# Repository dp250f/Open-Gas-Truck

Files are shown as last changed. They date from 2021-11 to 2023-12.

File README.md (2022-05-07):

# Open-Gas-Truck

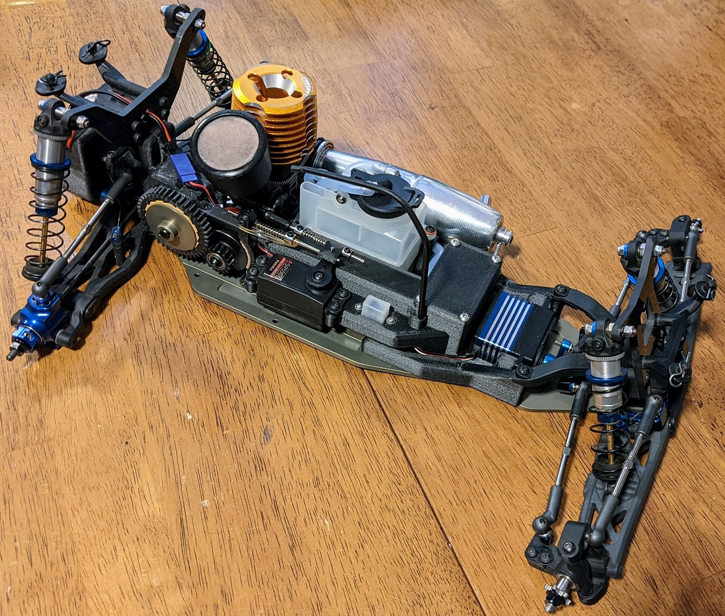
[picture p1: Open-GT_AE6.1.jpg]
Open-GT_AE6.1


The original open-source gas truck conversion

## Associated T6 Series Gas Truck Conversion

There are separate sections and guides for each of these items:

* [3D-Printed parts](3D-Printed)
* [Laser-Cut parts](Laser-Cut-Parts)
* [Modified parts](Modified-Parts)
* [Purchased parts](Purchased-Parts)
* [Assembly](Assembly)

Here's the Fusion 360 (CAD) shares:

* [Full Assembly](https://a360.co/3vGxaeg)
* [Chassis Template Drawing](https://a360.co/3ybymYJ)
* [Laser-Cut Engine Mount Drawing](https://a360.co/3vRHFeG)
* [Laser-Cut Engine Mount Shim Drawing](https://a360.co/3vJ6Rnu)

## Description

How to make your own gas truck conversion. Currently only the Associated T6 platform is done. TLR 22T conversion may happen if I or someone else feels very motivated and has the time to do so.

## Getting Started

First I must say this is a project for experienced makers/hobbyists. There may eventually be ready-to-assemble kit versions, but for now it's DIY only.

### Prerequisites

* 3D printer(s) with the following capabilities (for printing carbon-fiber PA6 Nylon)
    * Hard 0.4mm and 0.25mm nozzle (hardened steel or equivalent)
    * 300°C capable hot-end (make sure you hot-tighten it at that temperature)
    * Heated bed
* Filament dryer
* High quality Carbon-Fiber filled PA6 filament (I used Polymaker Polymide CF-PA6)
* Magigoo or equivalent PA bed adhesive
* Access to a laser cutting service such as send-cut-send
* A T6, 6.1, 6.2, or 6.3 you don't mind sacrificing to the gas truck gods :-)
* Lots of patience and some hacking skills

### Tools

* Printer for printing out chassis modification template
* Center-punch
* Cordless drill
* 3mm and stepped drill bits
* Countersinking bit
* High quality 3mm x 0.5mm tap and tap wrench
* Jigsaw with metal cutting blade
* Assorted files (round and flat)

## Authors

### Contributors names and contact info - *Contributions are welcome!*

* Damon Palm

## Version History

* 0.1
    * Initial Release

## License

This project is licensed under the **GNU General Public License v3.0 License** \- see the [LICENSE File](/LICENSE) for details

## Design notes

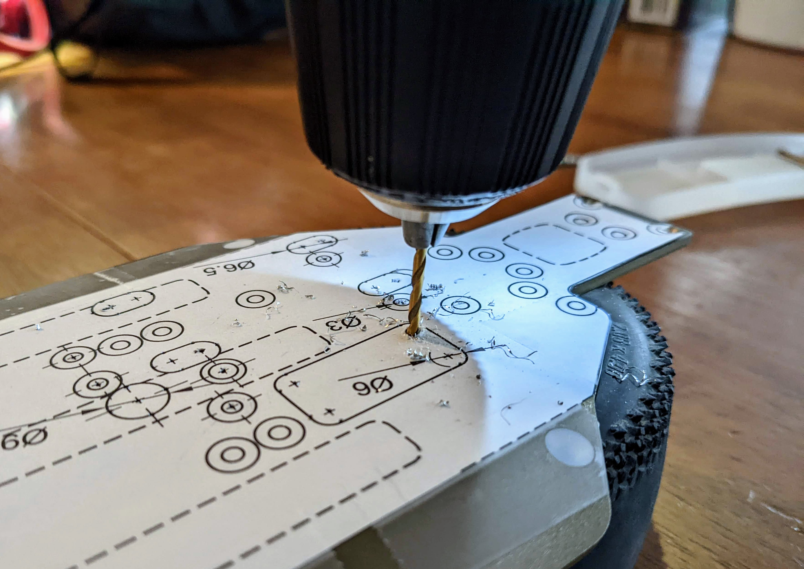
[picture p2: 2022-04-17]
Modified-Parts/Images/Chassis_Drill-1.jpg

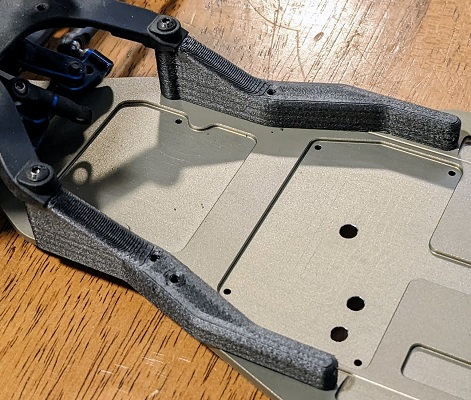
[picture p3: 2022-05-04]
Assembly/Images/FrontChassisBraces.jpg

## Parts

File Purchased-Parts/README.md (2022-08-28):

# Purchased Parts

## Off the shelf parts you will need to complete this build
There are seperate folders and guides for each of these items:

* Associated RC10T6 series truck

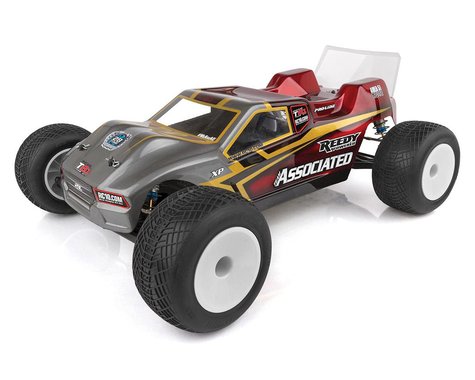
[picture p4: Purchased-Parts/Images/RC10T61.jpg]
RC10T6.1
  
* .12ci (2.1cc) Nitro engine
  * I used an **SH Engines .12 Pro Rear Exhaust Touring Car & Truck Nitro Engine (Turbo Plug)** (SHEPT12R02SXT-1). This is basically the same as the old Dynamite Platinum 12, but with a slide carburetor. It's easy to tune, runs smooth, and has plenty of power for a 2WD truck.

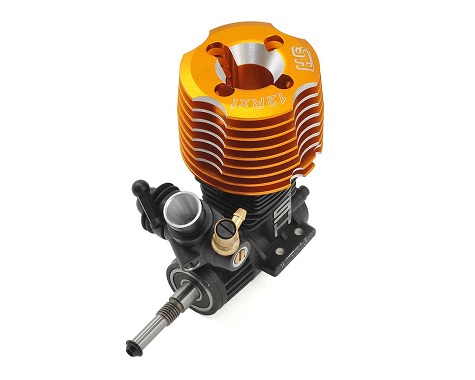
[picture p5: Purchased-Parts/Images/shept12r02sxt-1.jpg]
SHEPT12R02SXT-1
  
* Exhaust header/pipe
  * There are 2 gas truck exhausts currently being made: Ignite RC (IG006) and RD Logics (61900 and 61905). Novarossi still has some new old stock 1/10th pipes which will work with the RD Logics header.

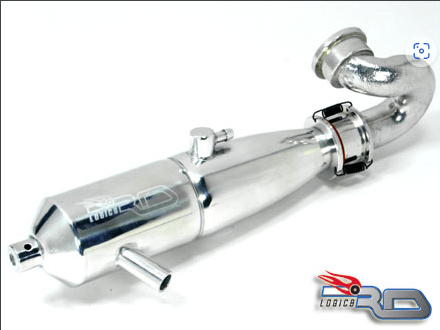
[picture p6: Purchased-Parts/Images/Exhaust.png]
Exhaust
  
* Air filter
  * I used a **Traxxas Complete Air Filter Set (TMX 2.5, 3.3)** (TRA5260). It might seem too large for this carburetor, but the included zip-tie clamps it down good and it seals fine. [Motorsaver.com](https://motorsaver.com/10scale.htm) also has some very nice 1/10th size filters for all sizes of carburetors.

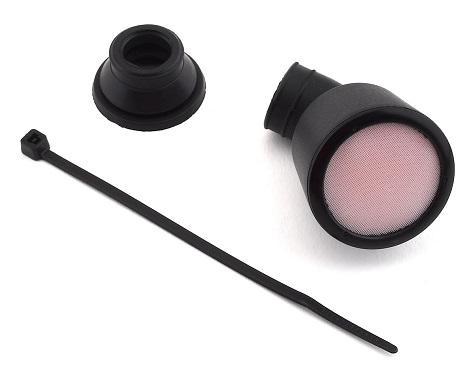
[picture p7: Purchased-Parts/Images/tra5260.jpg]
tra5260
  
* 75cc Fuel Tank (REDCAT 02004) These can be found on Amazon for around $10-$15. Make sure you get a genuine Redcat tank - I've had some cloned tank lids not seal at all.

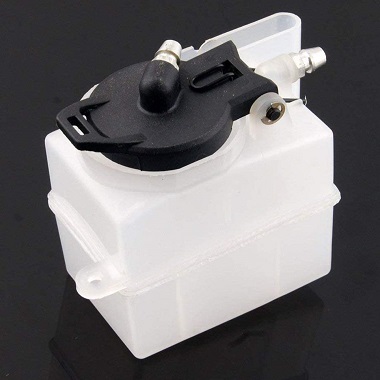
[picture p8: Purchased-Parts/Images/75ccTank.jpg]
75ccTank
  
* Fuel Filter
  * These tanks don't have filters, so this is necessary. I use a small Sullivan "Crap Trap" filter (SUL187).

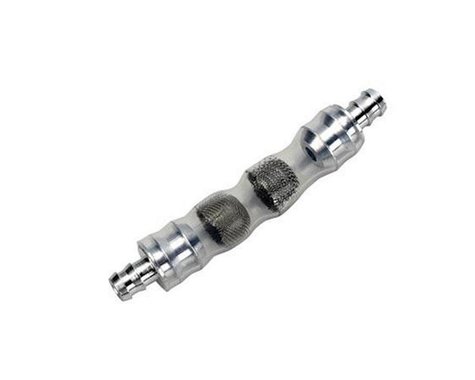
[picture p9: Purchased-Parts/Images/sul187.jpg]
sul187
  
* Standard size silicon fuel line

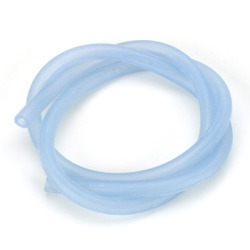
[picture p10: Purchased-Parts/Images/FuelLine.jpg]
FuelLine
  
* 32mm (Kyosho style) 1/8th scale clutch
  * I used a **Fioroni 32mm Quattro "Original RED" 4-Shoe Adjustable Clutch System** (FIO-OT-FR104-R). I've been very happy with this setup, and since it is standard 1/8th stuff, you have lots of tuning options.

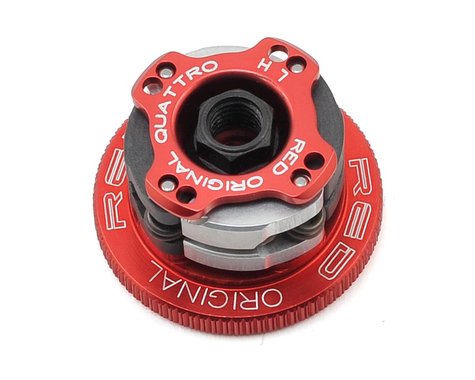
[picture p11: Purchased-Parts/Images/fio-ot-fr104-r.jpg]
fio-ot-fr104-r
  
* 16T Mugen/OFNA style clutch bell
  * I used a **ProTek RC Hardened Clutch Bell w/Bearings (16T) (Mugen/OFNA Style)** (PTK-7053) because it uses HUGE bearings which shouldn't wear out for a very long time.

  ptk-7053
* Team Associated B6.1/B6.1D Standup Top Shaft (ASC91798)

  asc91798
* Team Associated Throttle/Brake Linkage Set (ASC81251)
  * Other similar linkage sets might work, but I really can't say for sure.

  asc81251
* Silicon switch cover
  * I used a **Mugen Seiki Switch Cover** (MUGB0401). Other 1/8th offroad switch covers are likely to work also.

  mugb0401
* Receiver switch
  * I have a Sanwa receiver, so I used a Sanwa switch (SNW107A20064A). Since this kit uses LiPo receiver batteries, a charge plug is not necessary. I just plug the balance plug into my charger.

  snw107a20064a
* Receiver Battery (Mid - for smooth, high-grip tracks) - Mugen/AE/8ight-X style LiPo pack (85 x 30 x 17mm) - (PTK-5196)

  ptk-5196

* Receiver Battery (Rear - for lower-grip tracks) - HB/8IGHT style LiPo pack (39 x 56 x 21mm) - (PTK-5171)

  ptk-5171

* Screws
  * 1 M3x? button head hex screws
  * 1 M3x? countersunk flat head hex screws

* Receiver / Servos (low profile servo for throttle)

## Authors

Contributors names and contact info

So far it's just me here... Contributions are welcome!
Damon Palm

## Version History

* 0.1
    * Initial Release

## License

This project is licensed under the GNU General Public License v3.0 License - see the [LICENSE File](LICENSE) for details

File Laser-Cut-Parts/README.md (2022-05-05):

# Open-Gas-Truck

## Laser-Cut Parts instructions are waiting on parts.

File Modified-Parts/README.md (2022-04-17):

# T6.1 Chassis
## Intro
Time to bust out the center-punch, drill, jigsaw, metal files, and kiss your chassis goodbye!

Make no mistake, you may destroy a perfectly good chassis. Even if everything goes right, you probably won't be using it as an electric chassis again (the rearmost right-side waterfall mount hole is gone).

Basically, you'll be printing out a paper template, taping it to the chassis, marking the holes and cutout with the center-punch and sharpie, and hacking the chassis with power tools. Take your time and you won't need to do it more than once.

## Tools
* Metal center-punch
* Cordless drill or drill press
* 2mm, 3mm and stepped drill bits
* Countersinking bit
* Jigsaw with skinny blade that fits into a 1/4" hole
* Assorted files (round and flat)

## Work
* Download and print the chassis template PDF at 100% scale
* Cut it out and tape it to the bottom of your chassis, making sure existing holes line up
Chassis Template

* Sit the chassis on something solid and use a center-punch to all mark hole centers and edges of larger holes and slots

  Chassis CenterPunch

* Drill all hole centers with smaller drill bit, then drill them to final size with the 3mm drill bit

  Chassis_Drill-2

* Use a stepped drill bit to drill larger holes, engine mount slot ends, and corners of flywheel cutout

  Chassis Drill-3
* Use a countersinking bit to countersink all screw holes. Check fitment of each hole with a screw making sure it sits flush in each hole

  Chassis Screw-Fit
* Use a countersinking bit to deburr both sides of each hole
* Use a sharpie to mark the edges of the flywheel cutout and engine mount slots

  Chassis Countersink
* Use a jigsaw to cut out flywheel hole and engine mount slot edges

  Chassis Saw-2
* Use metal files to smooth and deburr flywheel cutout and engine mount slots

  Chassis File
* sit back and admire your handy work!

## Authors

Contributors names and contact info

So far it's just me here... Contributions are welcome!
Damon Palm

## Version History

* 0.1
    * Initial Release

## License

This project is licensed under the GNU General Public License v3.0 License - see the [LICENSE File](LICENSE) for details

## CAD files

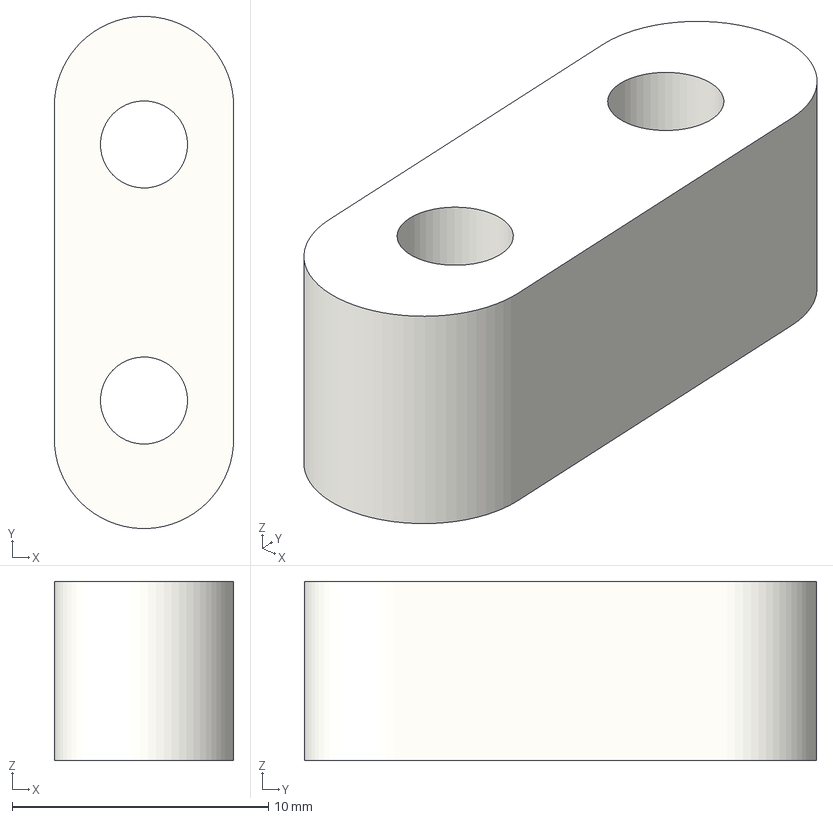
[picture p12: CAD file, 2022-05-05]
3D-Printed/BigNozzle/Throttle Servo Spacer.3mf
7.00 x 20.0 x 7.00 mm

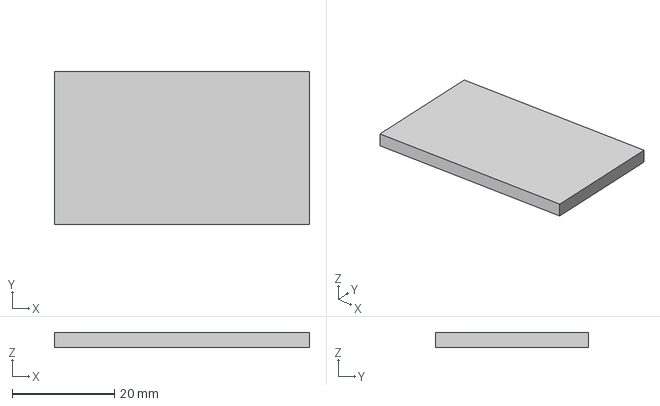
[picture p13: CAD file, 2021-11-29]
3D-Printed/Bridge-Test.3mf
50.0 x 30.0 x 3.00 mm

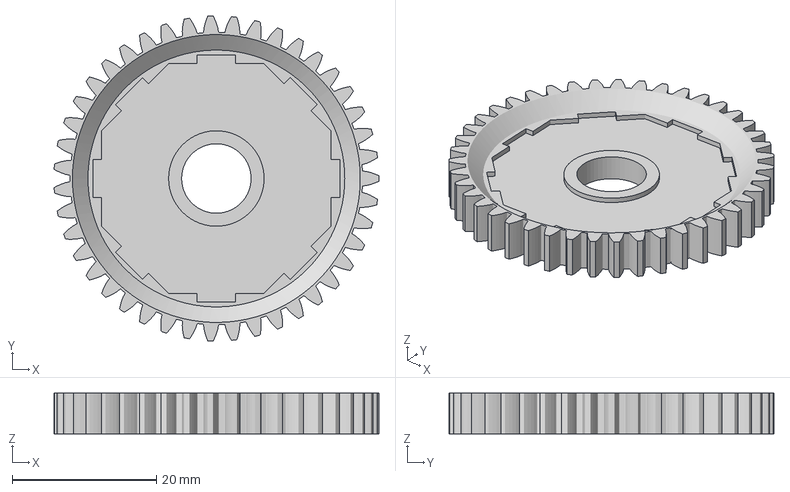
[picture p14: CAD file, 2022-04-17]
3D-Printed/SmallNozzle/Spur Gear (43 teeth).3mf
45.0 x 45.0 x 5.65 mm

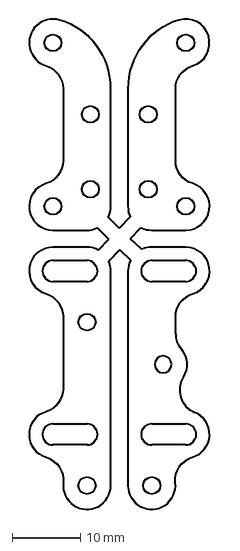
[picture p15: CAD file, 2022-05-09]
Laser-Cut-Parts/Laser-Cut Engine Mounts.dxf
27.1 x 72.6 mm

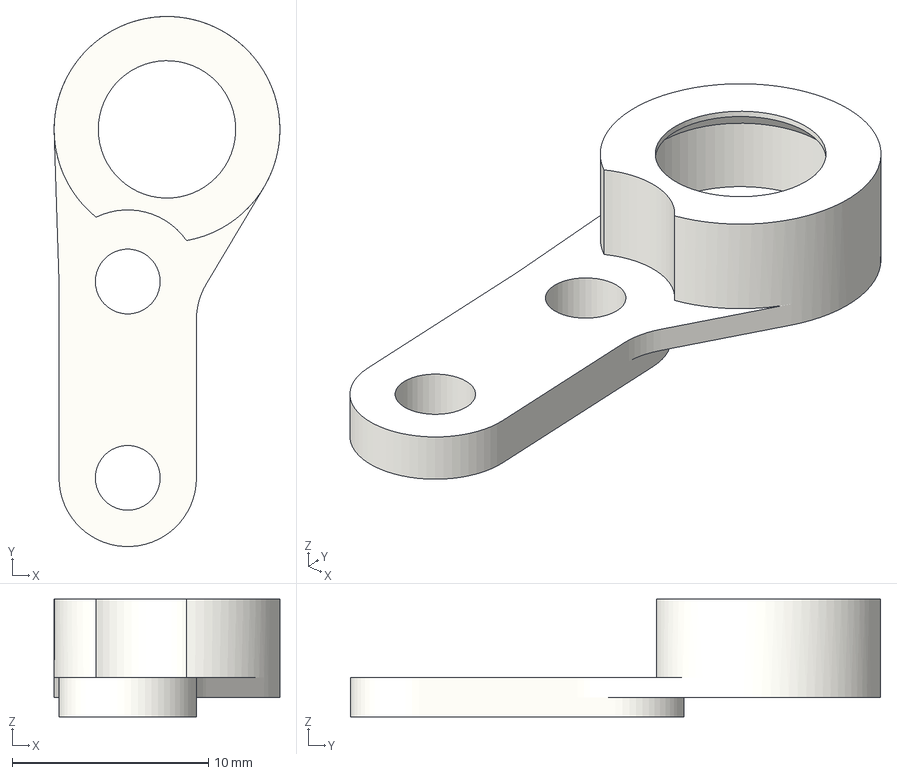
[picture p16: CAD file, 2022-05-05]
3D-Printed/BigNozzle/Spill tube stay.3mf
11.5 x 27.0 x 6.00 mm

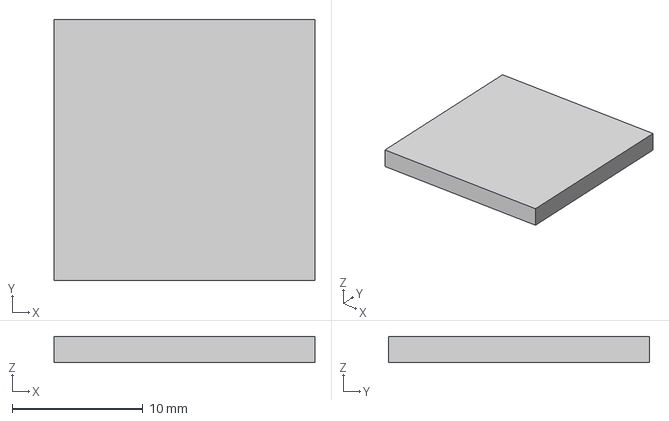
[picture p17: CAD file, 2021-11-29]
3D-Printed/Extrusion-Test.3mf
20.0 x 20.0 x 2.00 mm

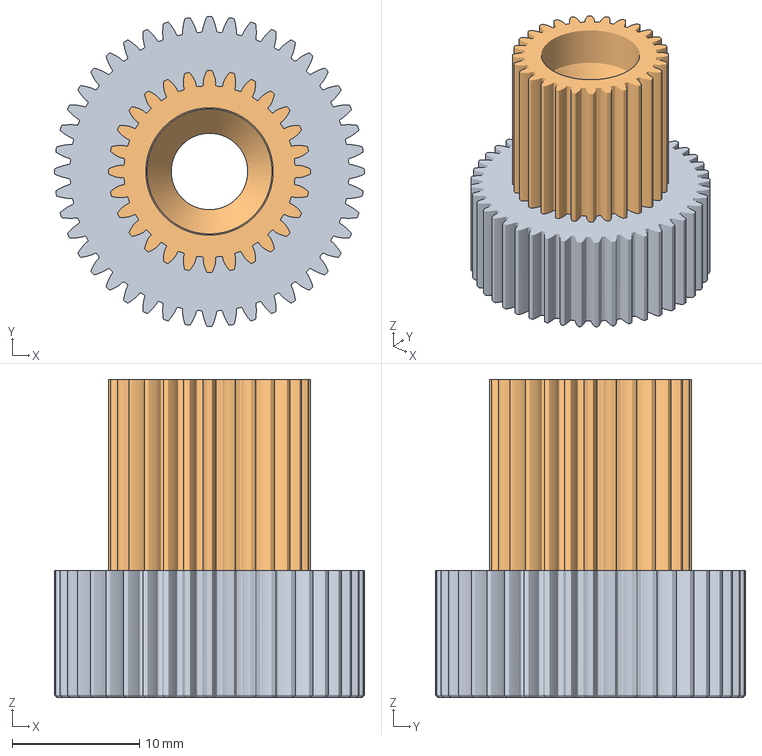
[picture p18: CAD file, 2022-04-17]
3D-Printed/SmallNozzle/Idler Gear.3mf
24.3 x 24.3 x 25.0 mm

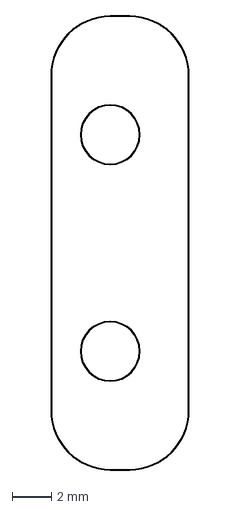
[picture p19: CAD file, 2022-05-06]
Laser-Cut-Parts/Laser-Cut Engine Mount Shim.dxf
7.00 x 23.0 mm

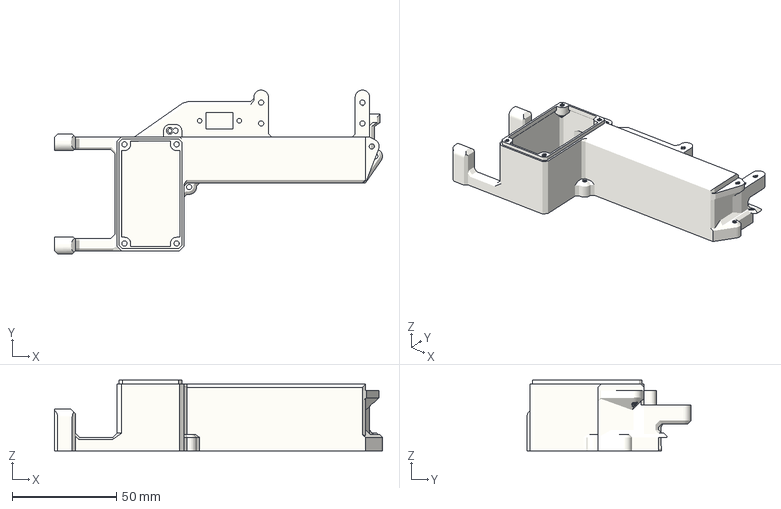
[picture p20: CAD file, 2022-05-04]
3D-Printed/BigNozzle/Electronics tray.3mf
157.1 x 78.5 x 34.0 mm

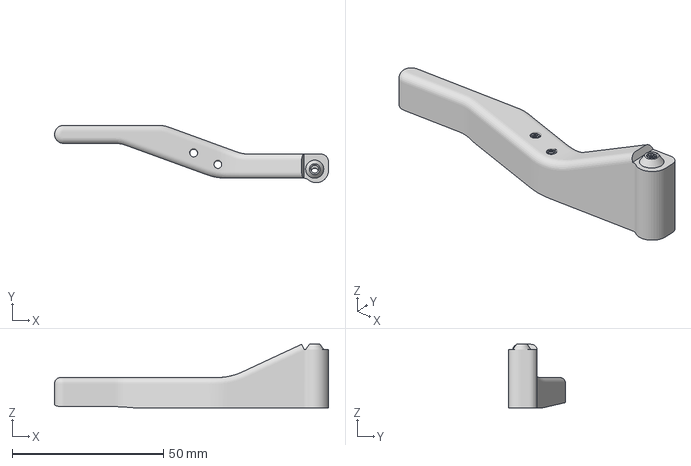
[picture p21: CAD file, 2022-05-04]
3D-Printed/BigNozzle/Front left chassis brace.3mf
90.6 x 19.0 x 21.0 mm

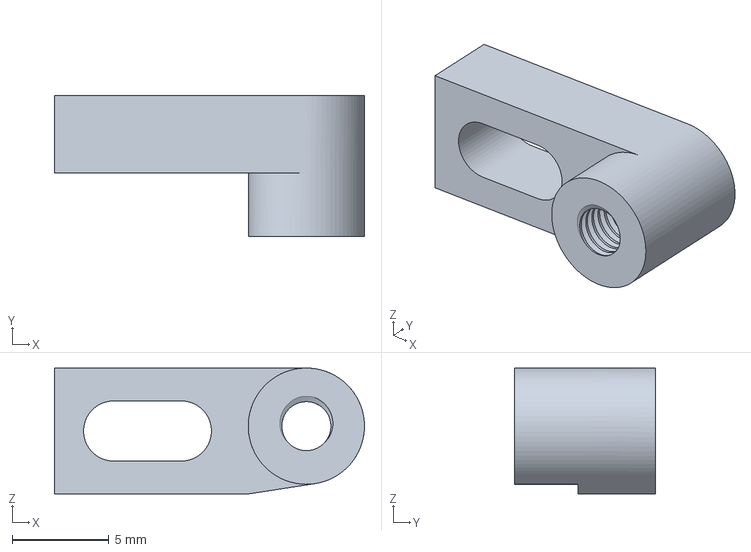
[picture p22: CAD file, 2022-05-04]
3D-Printed/BigNozzle/Brake Mount.3mf
16.0 x 7.27 x 6.50 mm

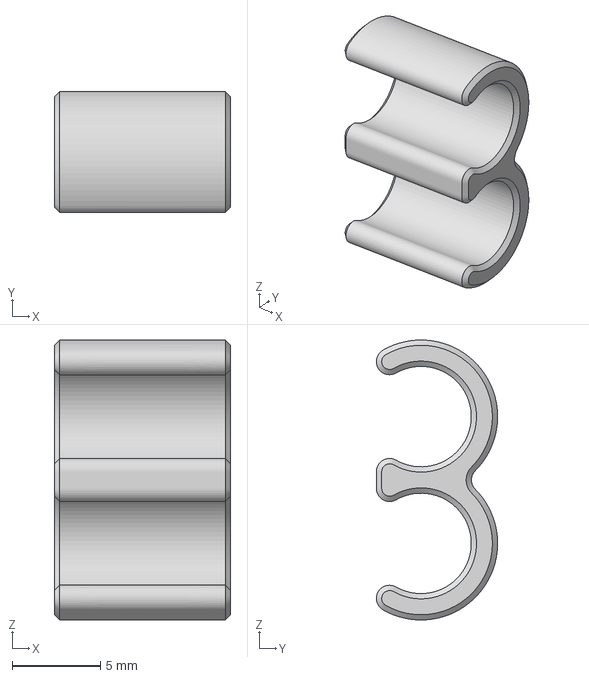
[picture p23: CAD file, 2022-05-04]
3D-Printed/BigNozzle/Fuel line clip.3mf
10.0 x 6.89 x 15.9 mm

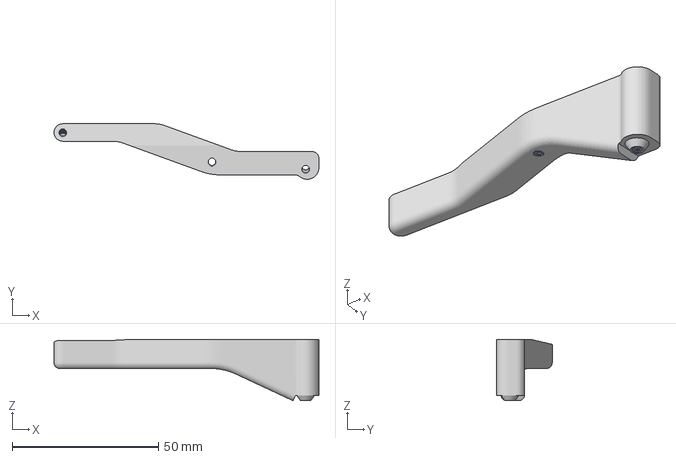
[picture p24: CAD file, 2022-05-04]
3D-Printed/BigNozzle/Front right chassis brace.3mf
90.6 x 19.0 x 21.0 mm

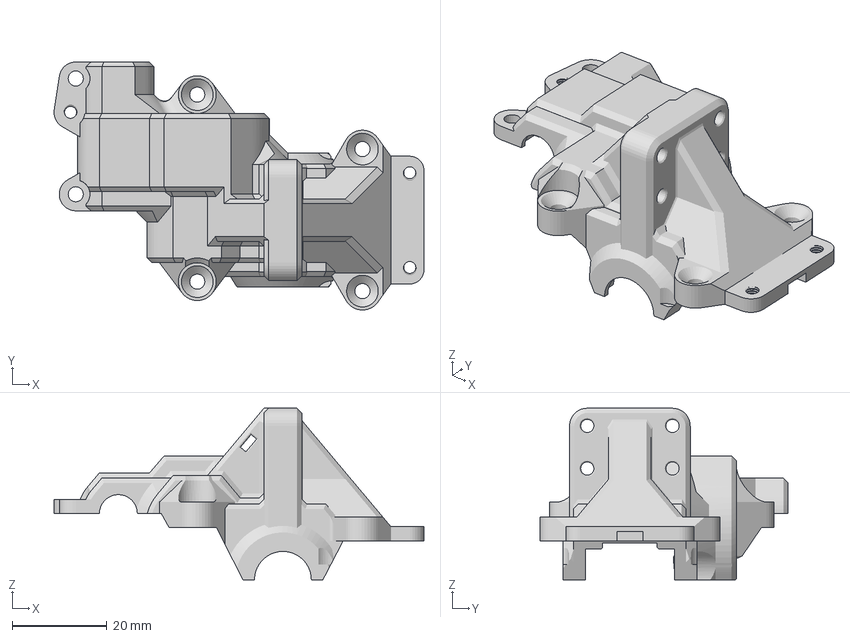
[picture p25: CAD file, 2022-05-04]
3D-Printed/BigNozzle/Transmission top.3mf
78.1 x 52.4 x 36.2 mm

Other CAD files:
3D-Printed/BigNozzle/Servo slider.3mf
3D-Printed/BigNozzle/Rear fuel tank mount.3mf
3D-Printed/BigNozzle/Transmission bottom.3mf
3D-Printed/BigNozzle/Battery box bottom.3mf
3D-Printed/BigNozzle/Battery box top.3mf
3D-Printed/BigNozzle/Chassis Shim.3mf
3D-Printed/BigNozzle/Front fuel tank mount.3mf
3D-Printed/BigNozzle/Receiver Cover.3mf
3D-Printed/BigNozzle/Transmission brace.3mf
3D-Printed/BigNozzle/brake lever.3mf

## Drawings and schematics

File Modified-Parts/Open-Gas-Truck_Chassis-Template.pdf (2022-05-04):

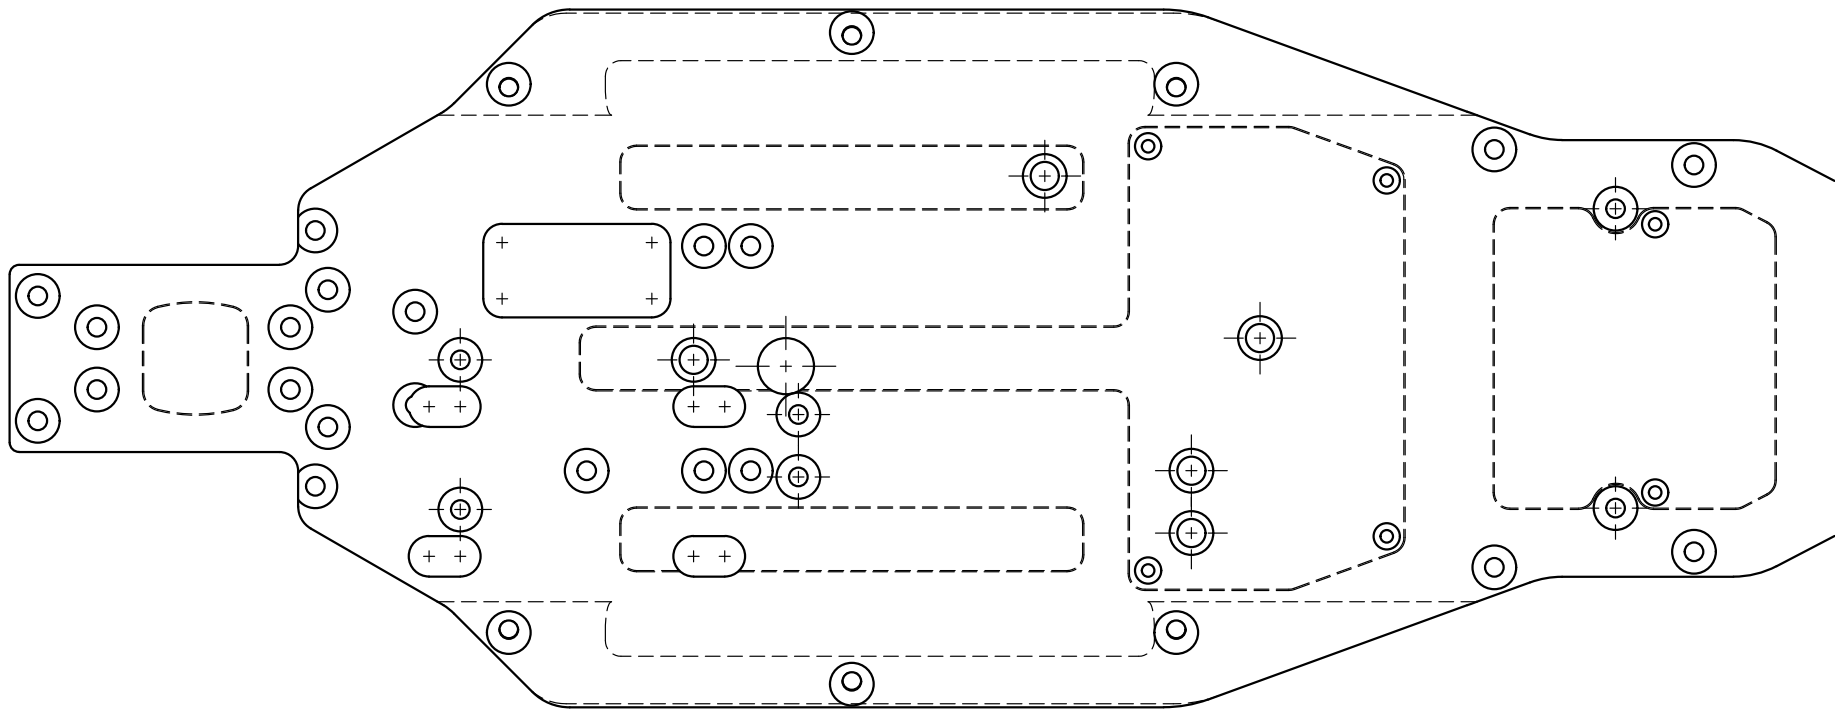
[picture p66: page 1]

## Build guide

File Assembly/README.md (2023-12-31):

# Assembly Guide

## Screw Sizes
Screw lengths are referenced in each step of this guide. Here's how to measure each type of screw
* Countersunk
  * Measure the whole screw

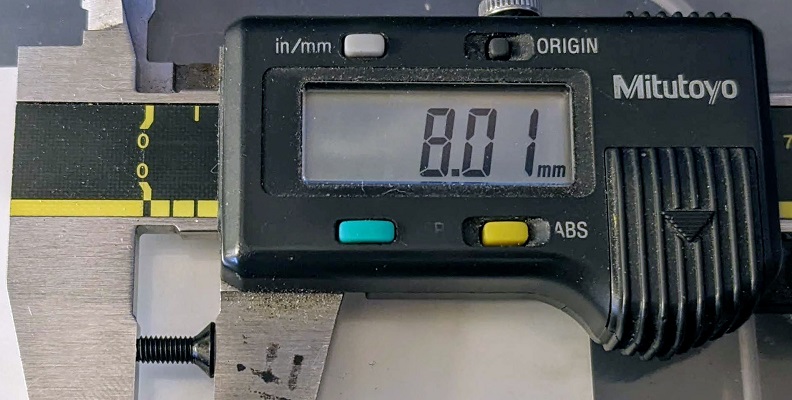
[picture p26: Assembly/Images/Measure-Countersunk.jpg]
Measure-Countersunk
  

* Button Head
  * Measure threads only

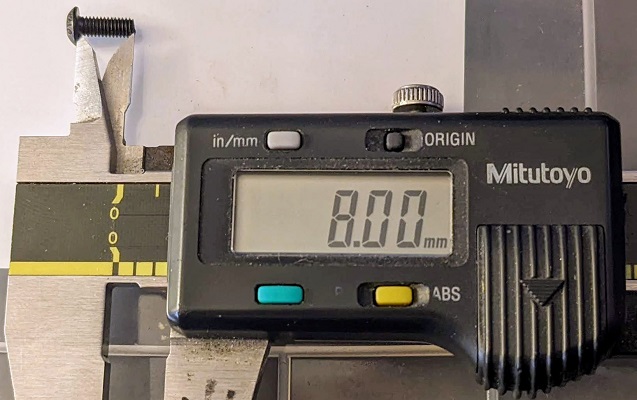
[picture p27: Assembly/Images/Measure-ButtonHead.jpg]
Measure-ButtonHead
  

* Cap Head
  * Measure threads only

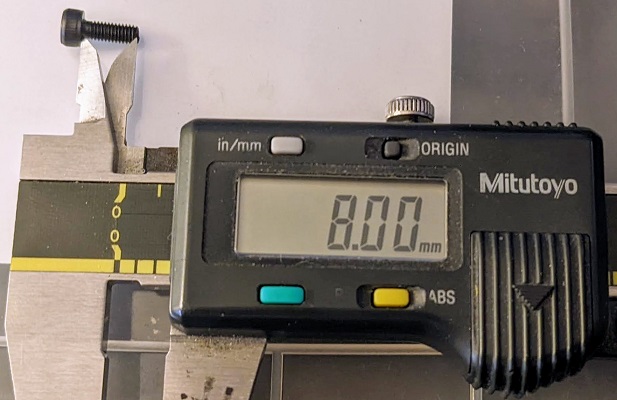
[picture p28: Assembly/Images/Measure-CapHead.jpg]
Measure-CapHead
  

# Front End Assembly

## Install Front Chassis Braces
  * Screws - (4) M3 x 10mm countersunk (front 2 holes)
  * Screws - (2) M3 x 8mm countersunk (rear hole)

## Install Front Clip and Bumper
  * Screws - (4) M3 x 16mm countersunk (bottom)
  * Screws - (2) M3 x 12mm button head (top)

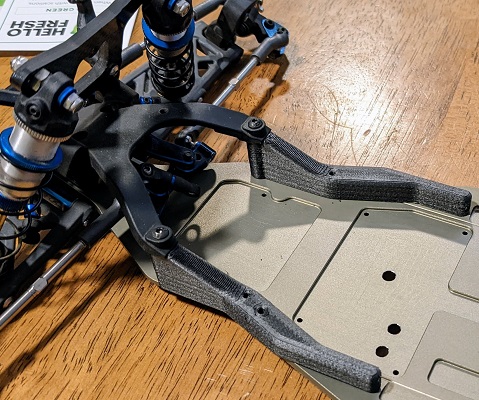
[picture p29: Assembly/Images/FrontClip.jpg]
FrontClip
  

# Rear End Assembly

## Assemble Slipper and Top Shaft
* Insert 3/16 x 3/8 bearing into spur gear

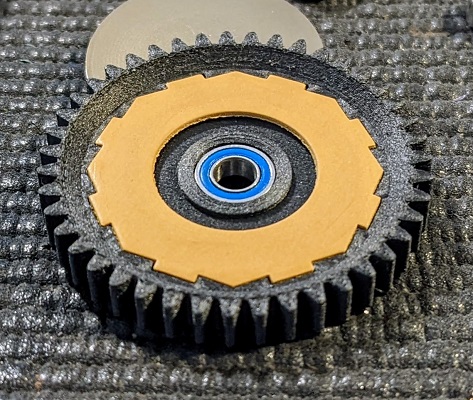
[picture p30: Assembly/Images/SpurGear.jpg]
SpurGear


* Assemble slipper and 3-gear (shorter) top-shaft with spur gear offset facing the inner slipper plate

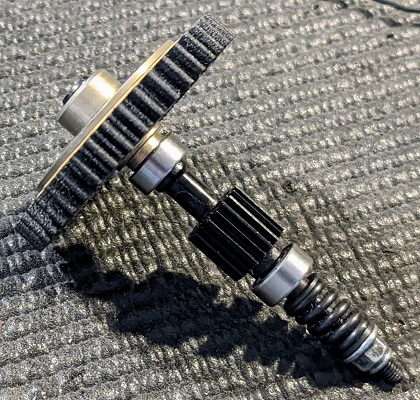
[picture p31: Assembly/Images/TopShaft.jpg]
TopShaft


## Assemble Transmission
  * Screws - ( 1) M2.5 x 8mm countersunk
* Install camber link block in bottom transmission case

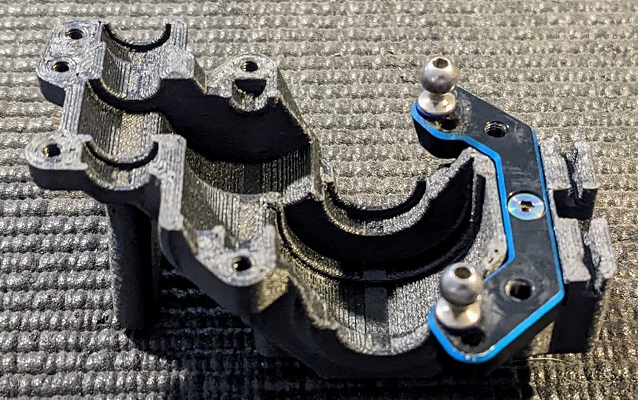
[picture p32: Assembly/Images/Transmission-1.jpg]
Transmission-1


* Install idler shaft and 5x10x4 bearings into idler gear

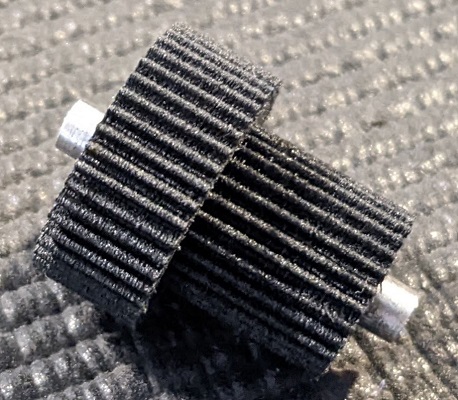
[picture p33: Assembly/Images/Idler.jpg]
Idler


* Install differential, idler, top-shaft, and swaybar in bottom transmission case and grease gears with black grease

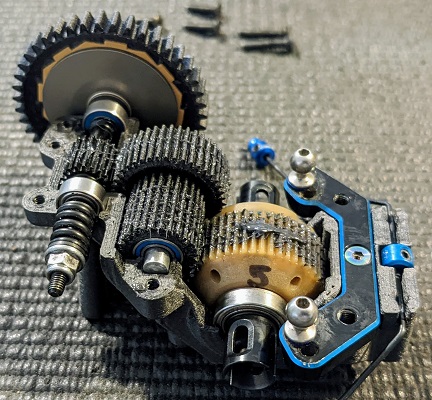
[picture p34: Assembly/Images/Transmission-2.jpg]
Transmission-2


  * Screws - (2) M3 x 16mm countersunk (rear)
  * Screws - (2) M3 x 12mm countersunk (middle)
  * Screws - (2) M3 x 8mm button head (front)
* Install top transmission case and screws

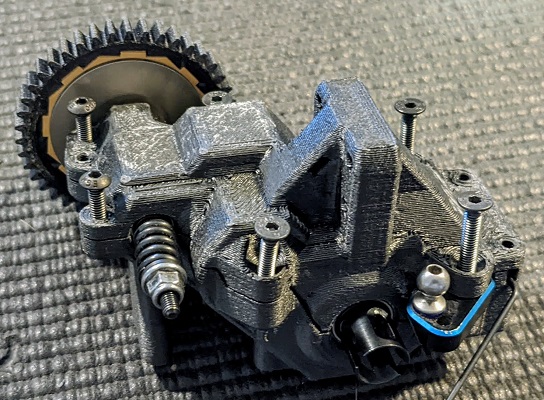
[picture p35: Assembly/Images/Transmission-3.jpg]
Transmission-3


## Install C-Block
  * Screws - (2) M3 x 6mm countersunk

## Install Transmission and Rear Shock Tower
  * Screws - (3) M3 x 10mm countersunk (front 3 transmission screws)
  * Screws - (4) M3 x 12mm button head (shock tower)
    
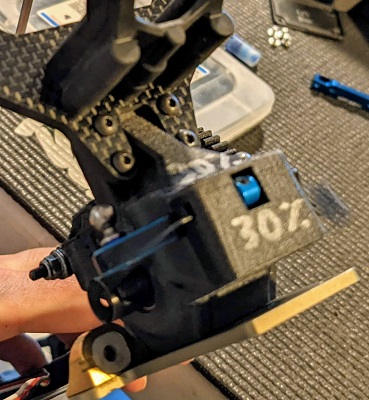
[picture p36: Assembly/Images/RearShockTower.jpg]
RearShockTower


## Install Transmission and Suspension (Mid-Battery Option)    
  * Screws - (2) M3 x 16mm countersunk (rear D-Block screws)
  * Screws - (2) M3 x 6 button head (swaybar screws)
* Secure D-Block and bumper using 16mm countersunk screws.
* Insert swaybar screws far enough to take slop out of the swaybar while allowing it to swing freely

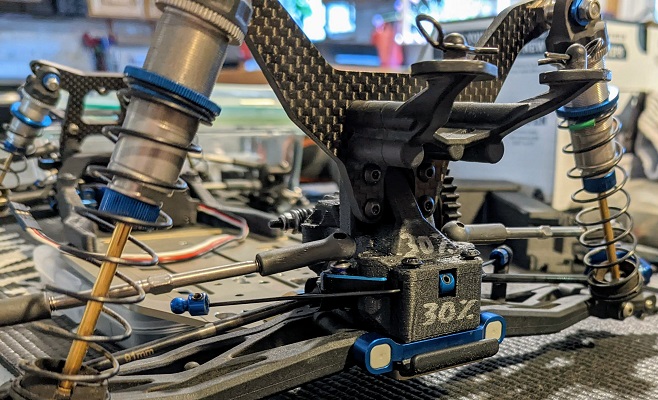
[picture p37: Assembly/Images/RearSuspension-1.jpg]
RearSuspension-1


## Assemble Rear Battery Box (Rear-Battery Option)
* Wrap a layer of tape around the battery as needed to protect the shrink wrap and insert battery into top of battery box

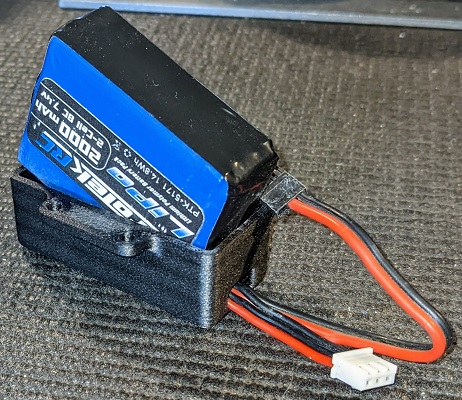
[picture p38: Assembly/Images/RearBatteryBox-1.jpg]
RearBatteryBox-1


  * Screws - (2) M3 x 8mm button head
* Screw battery box together

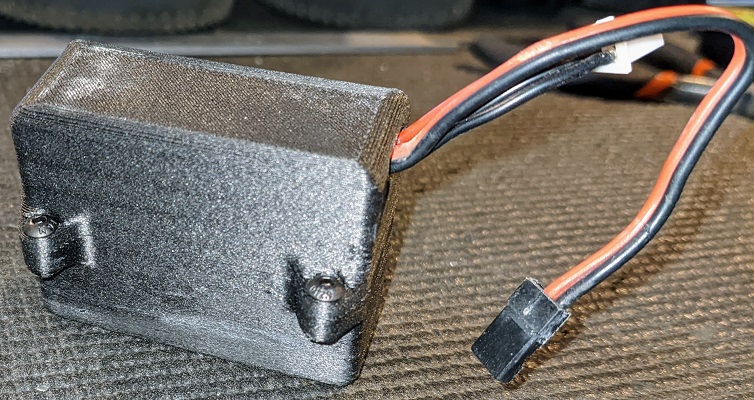
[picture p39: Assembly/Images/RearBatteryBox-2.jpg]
RearBatteryBox-2


## Install Rear Battery Box (Rear-Battery Option)
  * Screws - (2) M3 x 16mm countersunk (rear D-Block screws)
  * Screws - (2) M3 x 8 button head (top battery box mount)
* Attach bottom battery box where bumper normally goes using 16mm countersunk screws
* Use 8mm button head screws to secure top battery box in swaybar screw holes. These should get tight enough to take slop out of the swaybar while allowing it to swing freely while securing the battery box

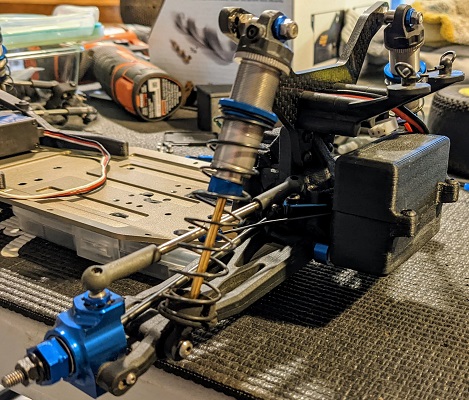
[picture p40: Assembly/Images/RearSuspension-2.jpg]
RearSuspension-2


# Electronics Tray Assembly

## Chassis Shims
* Glue chassis shims countersunk side down onto the 2 middle mounting holes as shown in the next step

## Install Mid Battery (Mid-Battery Option)
* Wrap a layer of tape around the battery as needed to protect the shrink wrap and insert battery into mid battery compartment

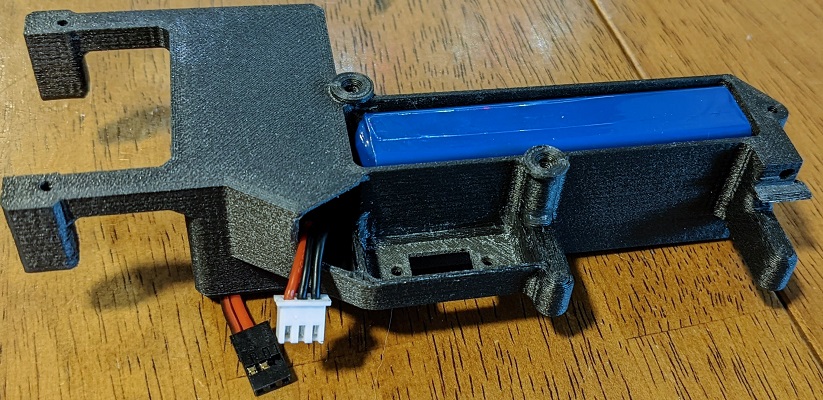
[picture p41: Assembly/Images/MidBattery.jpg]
MidBattery


## Install Steering Servo
  * Screws - (2) M3 x 10mm button head (top screws)
  * Screws - (2) M3 x 8 button head (bottom screws)
* Bottom side of servo should be flush or slightly higher than the bottom surface of the electronics tray

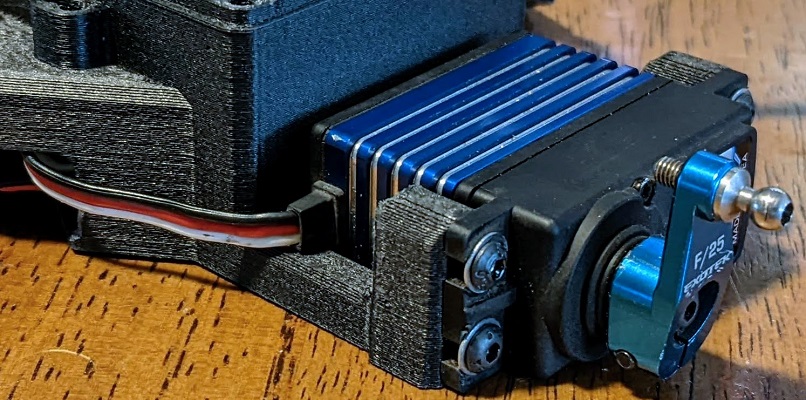
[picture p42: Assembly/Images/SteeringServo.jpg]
SteeringServo


## Install Switch and Throttle Servo
  * Switch screws - (2) whatever the switch came with
  * Screws - (4) M3 x 8-10mm button head (short throttle servo)
  * Screws - (4) M3 x 16mm button head (tall throttle servo)
    * Use Throttle Servo Spacers if using a tall servo
* Servo wire can tuck behind switch
* Switch wire tucks behind throttle servo (rear battery option)

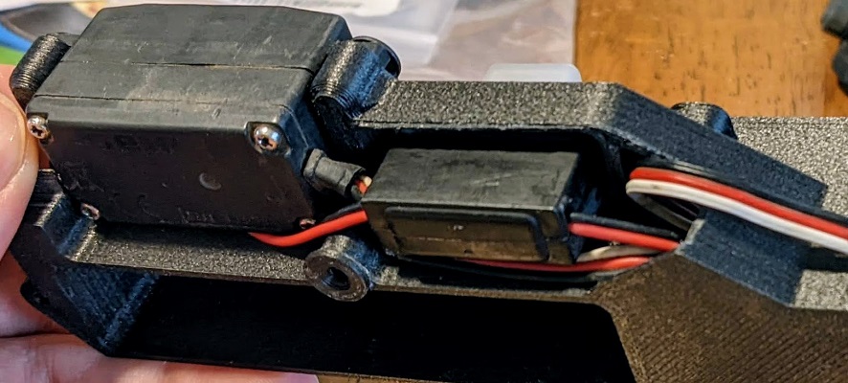
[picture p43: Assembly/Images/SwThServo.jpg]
SwThServo


## Install Receiver, transponder, antenna tube
  * Screws - (4) M3 x 6mm button head (receiver box cover)
  * Screws - (1) M3 x 4 set screw (antenna tube)
* Insert a layer of open cell foam in the bottom of the receiver box
* Plug switch, servos, and transponder into receiver

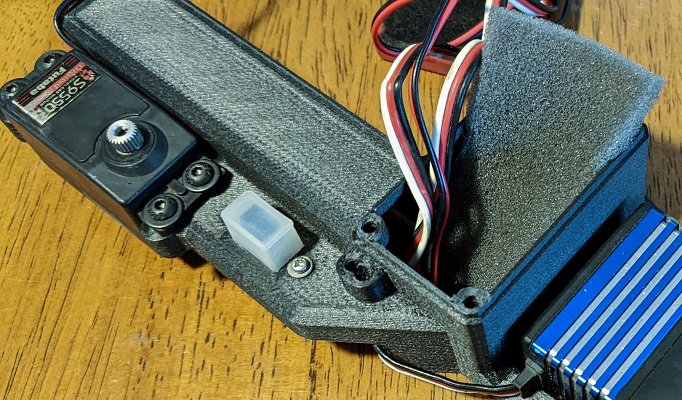
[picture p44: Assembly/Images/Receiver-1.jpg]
Receiver-1


* Feed antenna wire through antenna hole leaving enough slack to remove receiver from receiver box
* Feed antenna into antenna tube and install it using set screw
* Insert receiver, fold wires on top
* Insert transponder on top of wires

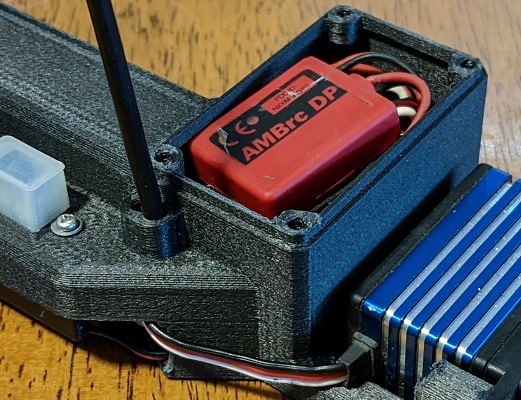
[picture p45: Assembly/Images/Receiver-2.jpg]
Receiver-2


* Insert a layer of open cell foam on top of transponder
* Install receiver box cover using button head screws

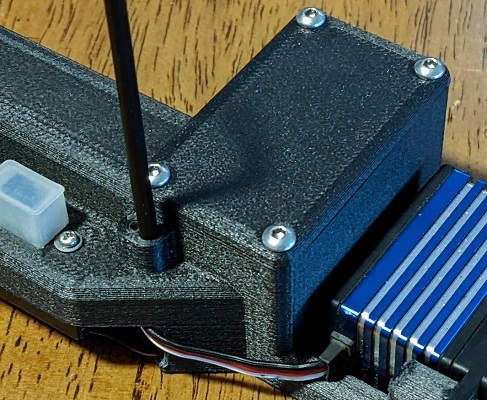
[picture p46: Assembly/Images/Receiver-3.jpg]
Receiver-3


## Assemble brake
  * Screws - (1) M3 x 16mm button head (brake arm)
  * Screws - (1) M3 x 12mm button head (brake mount)
* Cut out and glue 1/16" thick piece of cork onto brake arm (This is the brake pad)
* Drill brake linkage hole with 2mm drill bit (so a 2mm screw can rotate freely in it)

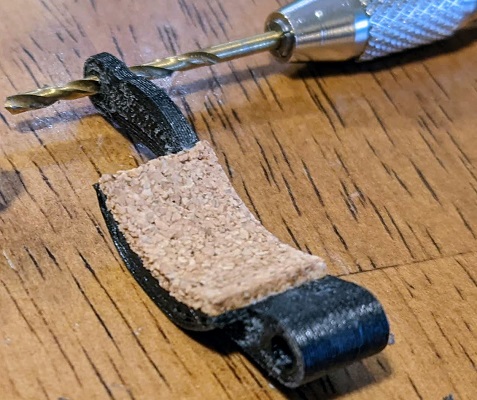
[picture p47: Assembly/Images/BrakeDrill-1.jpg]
BrakeDrill-1


* Drill brake pivot hole with 3mm drill bit (so a 3mm screw can rotate in it, but have almost no slop)

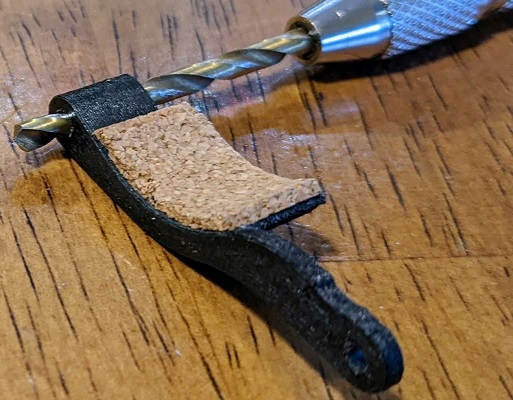
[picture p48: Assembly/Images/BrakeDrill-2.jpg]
BrakeDrill-2


* Assemble brake arm and brake mount using M3 x 16mm button head screw (Leave it loose enough to freely rotate)

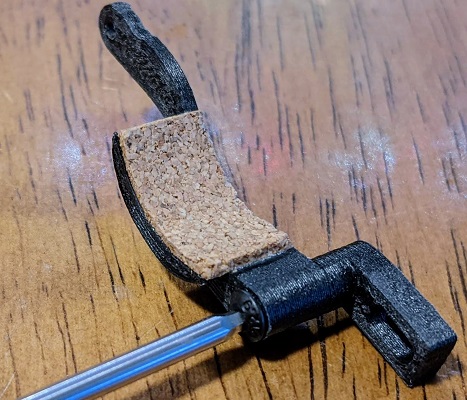
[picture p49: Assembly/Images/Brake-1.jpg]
Brake-1


* Assemble brake mount to electronics tray using M3 x 12mm button head screw (Leave it loose enough to be able to adjust the mount)

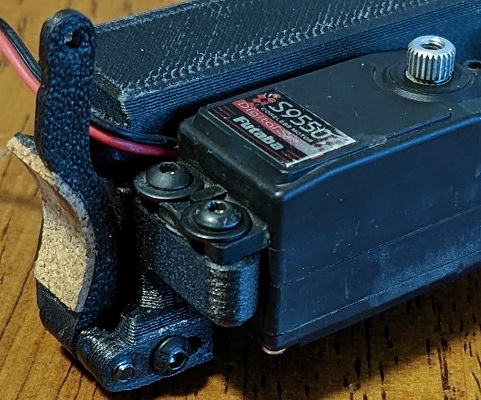
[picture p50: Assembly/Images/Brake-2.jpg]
Brake-2


# Center Chassis Assembly

## Install Electronics Tray
  * Screws - (5) M3 x 10mm countersunk
* Install electronics tray in chassis using countersunk screws
* Snap steering link ballcup onto servo arm ballstud

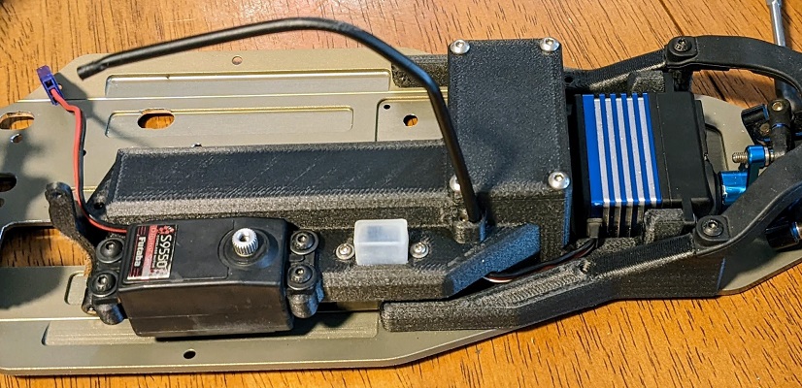
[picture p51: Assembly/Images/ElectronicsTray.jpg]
ElectronicsTray


## Install Transmission Brace
  * Screws - (2) M3 x 10mm countersunk
* Thread receiver switch wire and transmission brace through large heat shrink tubing (Rear battery option)
* Install transmission brace using countersunk screws
* Adjust slack in receiver switch wire, leaving room for brake lever to move all the way forward (Rear battery option)
* Shrink heatshrink using heat gun (Rear battery option)
* Secure receiver battery wire using small wire tie (Rear battery option)

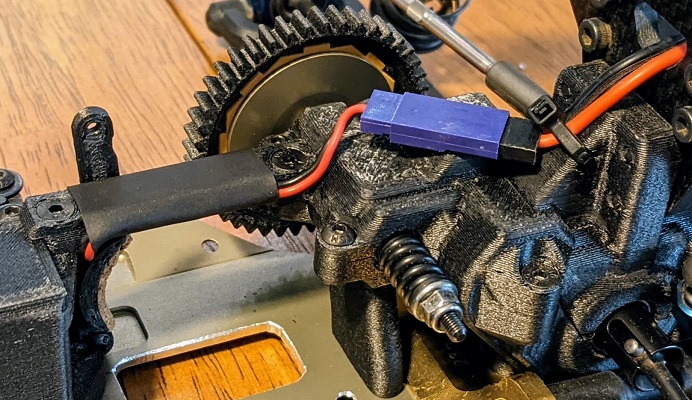
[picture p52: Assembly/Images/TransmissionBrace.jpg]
TransmissionBrace


## Install Fuel Tank
  * Screws - (2) M3 x 16mm button head (top fuel tank mounts)
  * Screws - (2) M3 x 8mm countersunk (fuel tank mount joiner)
  * Screws - (2) M3 x 12mm countersunk (fuel tank mount chassis screws)
  * O-Rings - (6) 1/10th scale shock o-rings (the kind that fit 3mm shock shafts)
* Cut slots in fuel tank lid to allow it to open all the way without bending the spring

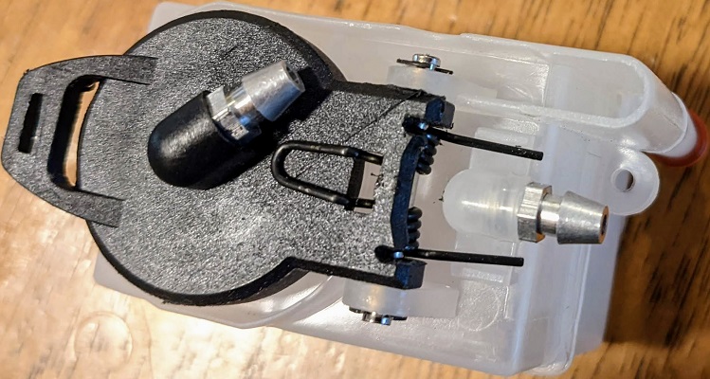
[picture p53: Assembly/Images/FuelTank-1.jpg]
FuelTank-1


* Drill mount holes with 3mm or 1/8" drill

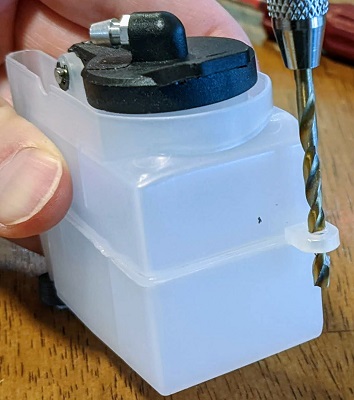
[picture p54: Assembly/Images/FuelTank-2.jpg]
FuelTank-2


* Install spill tube o-ring and spill tube stay

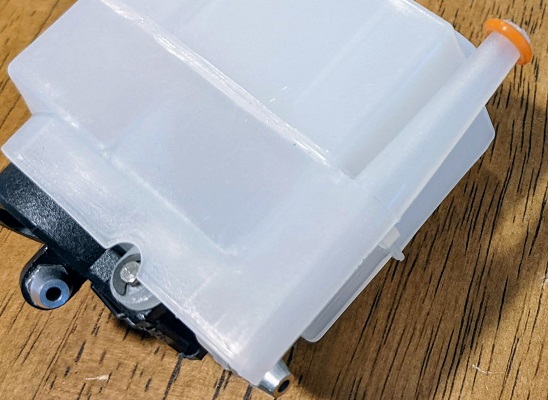
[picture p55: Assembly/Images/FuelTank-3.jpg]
FuelTank-3

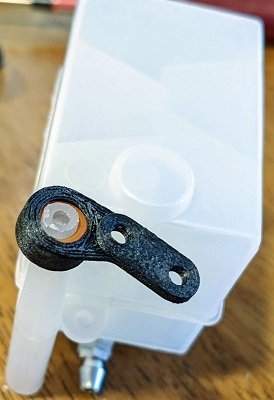
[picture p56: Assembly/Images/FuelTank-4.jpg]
FuelTank-4


* Attach front mount to tank using 16mm button head screw, 3 o-rings (2 bottom, 1 top), and washer
* Attach rear mount to tank using 12mm button hear screw, 2 o-rings, and washer

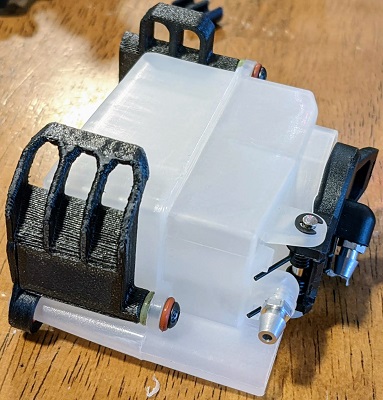
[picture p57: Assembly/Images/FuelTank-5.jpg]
FuelTank-5


* Attach tank mount joiner to tank mounts using (2) countersunk screws

* Install fuel tank in chassis using (2) countersunk screws

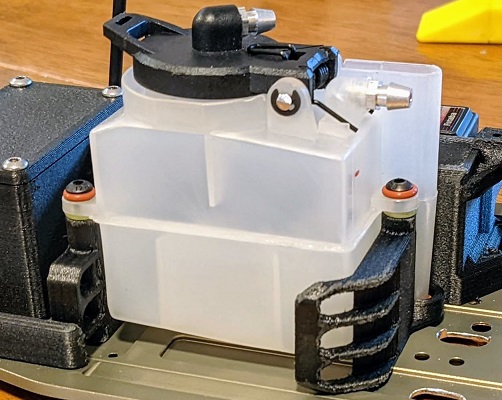
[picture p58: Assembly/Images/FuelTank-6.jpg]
FuelTank-6


# Engine Installation

## Assemble Engine, Clutch, and top Engine Mounts
  
  * Screws - (4) M3 x 12mm cap-head
* Install carburetor with slide facing the engine's left side and fuel fitting facing the rear of the engine
* Install clutch and clutch bell per clutch manufacturer's instructions
* Install throttle return elastic band
* Install air filter
* Install top engine mounts and shims as shown below using cap head screws **\*Use Threadlock**

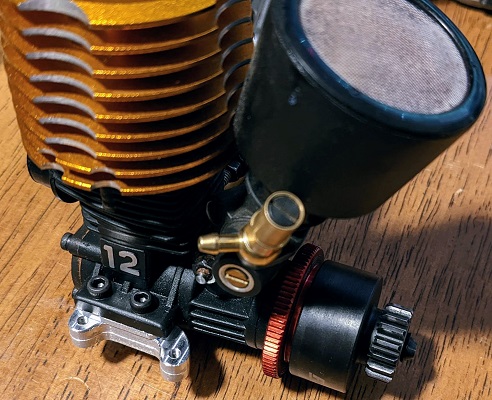
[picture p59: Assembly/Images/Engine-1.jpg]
Engine-1


## Install Bottom Engine Mounts

  * Screws - (4) M3 x 8mm countersunk
* Glue chassis shim to bottom front engine mount as shown below

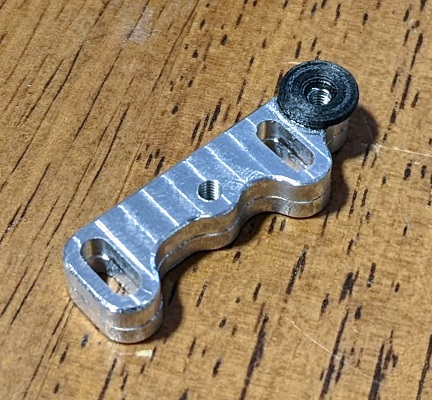
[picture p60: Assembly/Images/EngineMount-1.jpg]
EngineMount-1


* Install bottom engine mounts using countersunk screws **\*Use Threadlock**

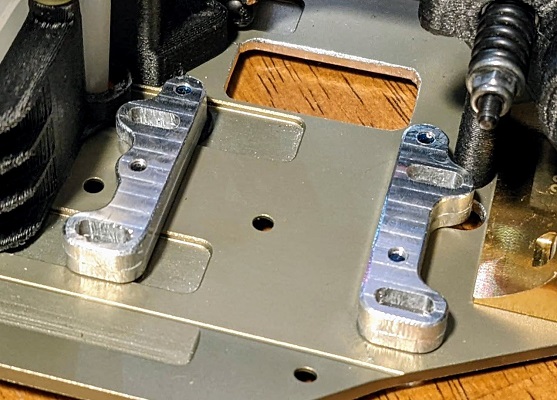
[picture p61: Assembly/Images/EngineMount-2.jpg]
EngineMount-2


## Install Engine, Fuel Line, Exhaust

  * Screws - (4) M3 x 12mm cap head
* Install engine using cap head screws from the bottom of the chassis
* Set gear mesh 
* **Threadlock** cap head screws one at a time
* Adjust brake and tighten brake mount screw

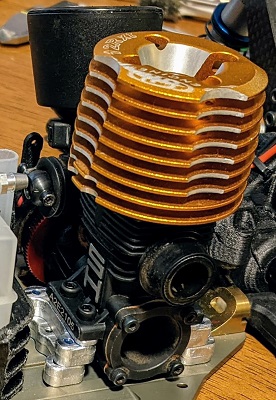
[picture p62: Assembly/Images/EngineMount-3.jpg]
EngineMount-3

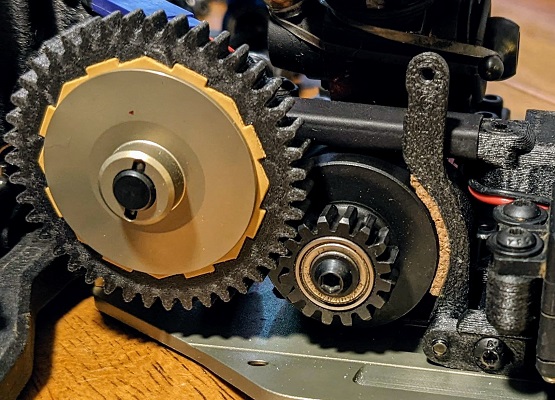
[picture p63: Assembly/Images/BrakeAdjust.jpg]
BrakeAdjust


* Install fuel line and fuel filter leaving enough free pressure line to connect the pipe later

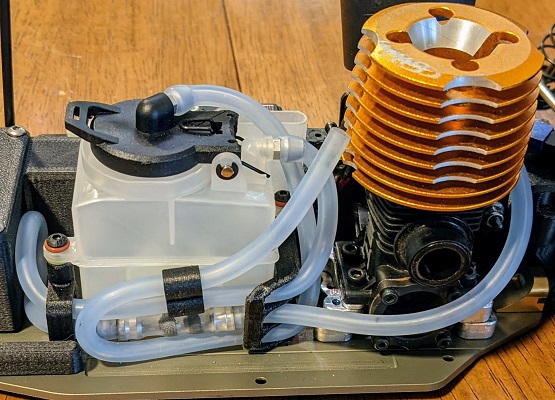
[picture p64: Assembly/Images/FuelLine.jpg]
FuelLine


  * Screws (1) M3 x 12mm button head
* Install Exhaust manifold and pipe. Secure pipe hanger wire with button head screw and washer

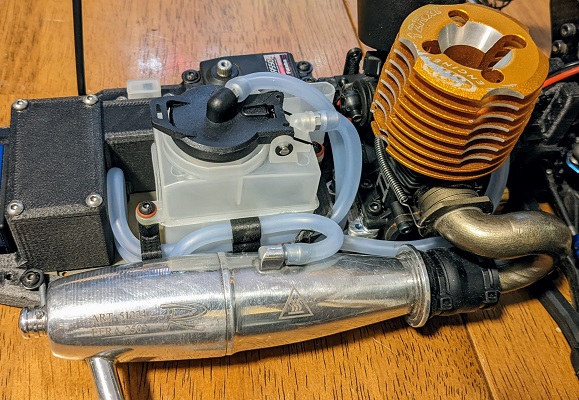
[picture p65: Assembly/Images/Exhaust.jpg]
Exhaust


## Install Throttle Linkage
  * Screws (2) M2 linkage screws (long and short)
* Drill out one throttle slider hole so your linkage slides freely through it.
* Attach throttle slider on top side of throttle servo arm (short servo option)
* Attach throttle slider on bottom side of throttle servo arm (tall servo option)
    * Leave it loose enough so it rotates freely on the arm.

Throttle-1

* Turn on Transmitter and receiver and center all throttle trims.
* Assemble throttle and brake linkage as shown below
* Throttle link slides through throttle slider. Use stiffer spring(s) on this one
* Brake link threads into throttle slider

Throttle-2
Throttle-3

https://github.com/dp250f/Open-Gas-Truck/assets/33988652/a270fac0-811a-4a7e-be5f-dab042d3d477

# 
## Authors

Contributors names and contact info

So far it's just me here... Contributions are welcome!
Damon Palm

## Version History

* 0.1
    * Initial Release

## License

This project is licensed under the GNU General Public License v3.0 License - see the [LICENSE File](LICENSE) for details

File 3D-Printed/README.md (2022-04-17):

# 3D Printed parts guides

## Description

Different types of parts have their own guides:

* *[0.4mm nozzle](BigNozzle/README.md)*
* *[0.25mm nozzle](SmallNozzle/README.md)*

## Prerequisites

The sizing of these parts and this guide assume you'll be using PrusaSlicer. You are free to use whatever slicer you want, but be warned - You'll be on your own to figure out what settings work. I started out using Cura, but couldn't get support material to work well while being reasonably easy to remove.

* 3D printer(s) with the following capabilities (for printing carbon-fiber PA6 Nylon)
    * Hard 0.4mm and 0.25mm nozzle (hardened steel or equivalent)
    * 300°C capable hot-end (make sure you hot-tighten it at that temperature)
    * Heated bed
* Filament dryer
* High quality Carbon-Fiber filled PA6 filament (I used Polymaker Polymide CF-PA6)
* Magigoo or equivalent PA bed adhesive

# Before printing parts...

Save yourself from future headaches by drying your filament and doing some tuning. This material prints very different than PLA. It's also expensive, so these test prints are pretty minimal.

## Tune Extrusion Multiplier

Because CF-Nylon likes to absorb moisture, it's nearly impossible to keep it completely dry without storing it in a vacuum chamber. I've also found my E-steps are off compared to PLA likely due to how hard this stuff is. Rather than throw off E-steps for printing other types of filament, it's easier to tune extrusion multiplier for this material (you'll need to even if you do re-tune your E-steps).
Extrusion Multiplier test prints

* Print small 20x20x2 calibration cubes at 100% infill to determine what multiplier to use. Make sure you use the same extrusion width, layer height, and infill/skin overlap settings you will be using to print your parts. (It shouldn't matter, but slicers be weird like that) You want a smooth top surface with no gaps and just a little bit of roughness that you can see and feel with your fingernail around the edges of the infill where it overlaps the perimeters.
* This can vary depending on how dry your filament is. 0.86 (or 86%) is the multiplier I ended up using after it's been out of the vacuum sealed packaging for a day or so (I don't have a vacuum chamber to store it in). In theory, if you can get this stuff completely dry and re-tune your E-steps, it'll be 1.00. I've never bene able to get higer than 0.87 with my filament dryer. I always store it in a sealed bag with desiccant in the box it came in and always print from the filament dryer (and leave it in there all day every time I do). I've found if I can't use at least 0.85 extrusion multiplier, that means it's too wet, will ooze like crazy and not have good layer adhesion.
* Dimensional accuracy is less important for most parts while layer adhesion is most important, so err on the side of over-extrusion.

## Tune Bridge Flow Ratio

CF-Nylon doesn't seem to exhibit die-swell and shrinking like PLA does, which makes bridging more difficult. Excellent bridging can still be accomplished with CF-Nylon, but it requires a much lower flow ratio than you're used to. It can also re-melt and warp/sag the bridging layer when printing the next layer - but there's a workaround for that which we should only need to use for printing the spur gear.
Bridge Flow Ratio test prints (Top)
Bridge Flow Ratio test prints (Bottom)
These were printed at 30mm/s bridge speed. First number is flow ratio percent and 2nd number is fan speed. The top piece is without bridge cooling for reference.

* Print 30x50x3 bridging test cubes with 0% infill and no support, 0 bottom layers, 2 top layers and 3 perimeters.
* Try different speeds and flow ratios with 100% bridge fan speed. Usually 20mm/s-30mm/s and 40%-70% flow ratio.
* I like to stop the test print a little more than half-way through the last layer so I can see both the bridging layer by itself and with the next layer on top of it.
* You want a flow ratio which produces the smoothest and flattest bridge and top layer as possible. In these pictures you can see that's probably somewhere around 55%-60%

## Authors

### Contributors - *Contributions are welcome!*

* Damon Palm

## Version History

* 0.1
    * Initial Release

## License

This project is licensed under the **GNU General Public License v3.0 License** \- see the [LICENSE File](/LICENSE) for details

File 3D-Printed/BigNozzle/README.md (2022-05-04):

# 0.4mm Nozzle Parts

## Material / part requirements:

* Carbon-Fiber PA6 Nylon (Polymaker Polymide CF-PA6)
* Filament dryer which can dry Nylon
* 0.4mm hardened nozzle at 300°C
* Magigoo PA on 45°C bed
* Print each part one at a time to keep the layer time as short as possible. This makes layer adhesion as strong as possible.

## Slicer settings:

Assuming your hot end is up to the task of printing abrasives at 300°C and you've got a filament dryer capable of drying Nylon, printing CF-PA6 Nylon isn't too tricky. The sizing of these parts and this guide assume you'll be using PrusaSlicer. 
Here's the general slicer settings I use:

* Nozzle - 300°C
* Bed - 45°C
* Part cooling fan off (100% for bridging **ONLY**)
* Minimum layer time - 0 seconds (PrusaSlicer calculates whacky layer times when generating support material)
* 1.4mm retraction (This works on my MK3S extruder with an E3D Volcano and Nozzle-X)
* Extrusion Width - 0.5mm for everything except support material which is 0.4mm
* Layer Height - 0.15mm-0.25mm (I used 0.25mm for most parts)
    * Using a 0.5mm extrusion width allows up to 0.25mm layer height while maintaining good layer adhesion
    * I've not really noticed reduced layer adhesion within this layer height range.
* Perimeters - 4 (2mm)
* Top/Bottom layers - 1 (because 100% infill)
* Detect thin walls
* Detect bridging perimeters
* Don't support bridges
* 100% infill
* Support Contact Z Distance - 0.05mm (smaller gap improves layer adhesion with these layers)
* XY separation between an object and its support - 1.2mm to keep support from being printed in the middle of M3 threaded holes
* Print speed - 40mm/s-80mm/s (infill and support fast, small/external perimeters slow)
* Bridge speed - 30mm/s
* Bridge flow ratio - 0.55 (Whatever you arrived at with calibration prints)
* Extrusion Multiplier - 0.86 (Whatever you arrived at with calibration prints)

## Post-Processing

* There should not be blobs - if you see blobs, it's likely your hot end is leaking and needs to be hot-tightened. A loose hot end can cause all kinds of strange print quality issues.
* Remove support material as soon as possible
* You will find small pieces of plastic stuck to these prints. These should easily scrape off using a hobby knife and flat bladed screwdriver.
* Apply Medium or Thin CA glue to the bridge layers to strengthen parts where layer adhesion is less than optimal. Allow it to fully dry before assembly because it can leave a white residue on anything that is near it while it's drying.

Bridge Glue

* Cut away bridging layers which obscure holes. The purpose of these is to reduce support material.

Bridge Trim

## Rear Battery Box Top (Rear-Battery Option):

* All layer widths - 0.45mm (so the sides are 5 perimeters thick)
* No support Material
* 100% bridging fan
* Bridging angle - Set it to go across at 45°

Battery Box Top Orientation
Battery Box Top Preview

## Rear Battery Box Bottom (Rear-Battery Option):

* 0.2mm max layer height (better for overhangs)
* All layer widths - 0.45mm (so the sides are 5 perimeters thick)
* Support on build plate only (only on outside of part)
* 100% bridging fan

Battery Box Bottom Orientation
Battery Box Bottom Preview

## Transmission Case Top:

* Inside dimensions are critical on this part, so that side must face up
* Support on build plate only
* 100% bridging fan
* Bridging angle - Set it to go across the shortest edge

Transmission Case Top Orientation
Transmission Case Top Preview

## Transmission Case Bottom:

* Inside dimensions are critical on this part, so that side must face up
* Support on build plate only
* No part cooling

Transmission Case Bottom Orientation
Transmission Case Bottom Preview

### Transmission Cases Post-Processing:
* File smooth mating surfaces
* Glue Bridging areas

TransmissionCaseGlue

## Electronics Tray:

* Support on build plate only
* 5mm brim
* 100% bridging fan
* Bridging angle - Set it to go diagonal across large gaps

Electronics Tray Orientation
Electronics Tray Preview

### Post-Processing:
* Glue Bridging areas
* Remove bridging layer from switch cutout, screw holes, and antenna hole
* File brake mount area until brake mount fits flush with bottom

Brake Mount Fit

## Receiver Cover:

* No support Material
* No part cooling

Receiver Cover Orientation
Receiver Cover Preview

## Front Chassis Braces:

* Support on build plate only
* 30% Gyroid infill
* At least 1mm or 4 top and bottom layers
* No part cooling
* Print one at a time

Front Chassis Brace Orientation
Front Chassis Brace Preview

## Fuel Tank Mounts:

* Support on build plate only
* 30% Gyroid infill
* At least 1mm or 4 top and bottom layers
* No part cooling
* Print one at a time if needed to keep layer time under 60 seconds

Rear Fuel Tank Mount Orientation
Rear Fuel Tank Mount Preview

## Small Parts:

* Includes the following parts -
    * Brake lever
    * Brake Mount
    * Chassis shim (x4)
    * Fuel line clip
    * Servo slider
    * Tank mount chassis shim
    * Transmission brace
* No support Material
* No part cooling
* Print fewer parts at a time as needed to keep layer time under 60 seconds

Small Parts Orientation
Small Parts Preview

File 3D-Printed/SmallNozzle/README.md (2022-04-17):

# 0.25mm Nozzle Parts

## Material / part requirements:

* Carbon-Fiber PA6 Nylon (Polymaker Polymide CF-PA6)
* Filament dryer which can dry Nylon
* 0.25mm hardened nozzle at 300°C
* Magigoo PA on 45°C bed
* Print each part one at a time to keep the layer time as short as possible. This makes layer adhesion as strong as possible.

## Slicer settings:

Assuming your hot end is up to the task of printing abrasives at 300°C and you've got a filament dryer capable of drying Nylon, printing CF-PA6 Nylon isn't too tricky. The sizing of these parts and this guide assume you'll be using PrusaSlicer. 
Here's the general slicer settings I use:

* Nozzle - 300°C
* Bed - 45°C
* Part cooling fan off (100% for bridging **ONLY**)
* Minimum layer time - 0 seconds (PrusaSlicer calculates whacky layer times when generating support material)
* 1.4mm retraction (This works on my Printrbot extruder with an E3D V-6 and Nozzle-X)
* Lift Z on retract - 0.2mm
* Minimum travel after retraction - 1mm
* Extrusion Width - 0.3mm for everything except:
    * Support material - 90% (0.225mm)
    * Perimeters - 0.25mm
* Layer Height - I used 0.125mm (0.1 - 0.2)
* Perimeters - 5 (1.25mm)
* Top/Bottom layers - 1.5mm
* Avoid crossing perimeters
* Detect thin walls
* Detect bridging perimeters
* No support Material
* 20% or more Gyroid infill (only used on big side of the gear)
* Print speed - 40mm/s-80mm/s (infill and support fast, small/external perimeters slow)
* Bridge speed - 30mm/s
* Bridge flow ratio - 0.64 (Currently, lower values with this nozzle size cause PrusaSlicer to use this for solid infill also, which is BAD)
* Extrusion Multiplier - I used 0.86 (Whatever you arrived at with calibration prints)

## Post-Processing

* There should not be blobs - if you see blobs, it's likely your hot end is leaking and needs to be hot-tightened. A loose hot end can cause all kinds of strange print quality issues.
* You will find small pieces of plastic stuck to the inner surfaces. These should easily scrape off using the back edge of a hobby knife.
* If you find small pieces of plastic stuck to the outer surfaces, it should be easy to pick or scrape off with a hobby knife.
* Removing stray plastic from these pieces is critical to get the fit for bearings and gear mesh.

## Idler Gear:

* XY Size Compensation - I used -0.05 (usually between 0.00 and -0.07mm)
    * You'll need to test-fit this gear in the transmission to fine-tune this. It should be a tight mesh and feel like it needs to break-in a little. Only go negative on this one, and not so far you lose the 2nd perimeter in each gear tooth. If this is not enough to get the right fit, adjust your extrusion multiplier by 1% or 2%.
    * Make sure the idler gear fully meshes with the diff gear. The full height of the idler gear teeth should interlock with the diff gear teeth, not just the tops.
* No part cooling

Idler Gear Orientation
Idler Gear Preview
Idler Gear Mesh

## Spur Gear:

* XY Size Compensation - Same as you used for printing Idler Gear
* 100% bridging fan (layer adhesion isn't critical for this part)
* 100% fan on layer after bridging layer (This will keep bridge layer from warping)

    Add Custom G-Code
    * Move the top layer view slider (In PrusaSlicer) to the first layer after the bridging layer
    * Right-click the "+" and select "Add Custom G-Code"
    * Type 'M106 S255' and click OK (for single-extruder printers with Marlin firmware)
        * You can try slower fan speeds here as long as the underside stays flat after the next few layers
    * Move the top layer view slider (In PrusaSlicer) to the next layer
    * Right-click the "+" and select "Add Custom G-Code"
    * Type 'M106 S0' and click OK

* Bed adhesion is more difficult on this part. If you have trouble with it lifting off the bed, make sure your first layer has enough squish. Thoroughly clean the bed and use a fresh layer of Magigoo PA. You can also use less solid infill layers to decrease internal stresses. I recommend at least 4 top and bottom infill layers.

Spur Gear Orientation
Spur Gear Preview
